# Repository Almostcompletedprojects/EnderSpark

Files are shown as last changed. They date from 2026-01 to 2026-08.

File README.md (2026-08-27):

# WireEDM

Join the discord here: https://discord.gg/86cwKxkF

Wire EDM uses electrical discharges to cut any conductive materials (brass, steel, aluminium even tungsten carbide) with no mechanical forces, enabling high precision, deep cuts, and machining of hard or delicate materials without deformation. 
This project show how to build a DIY wire EDM machine using salvaged components from an old 3D printer and other affordable parts, keeping the total cost around 250€ + 4 machined parts the ender 3 and less than 50h of work (if everything goes right).

The machine's motion system is just an Ender 3  with 1:51 gear reductions on the X and Y axes. This is required for EDM because it's a slow process and and NEMA 17 on their own are too fast.
A Raspberry Pi Pico with a TC4428 and a powerful MOSFET are used to switch up to 10A at 60KHz

The toolpath generation is simplified to be user friendly and a small tutorial is available on this video: https://youtu.be/iLnna7q0drs?si=ul4SjGQGCm429spJ

And a complete tutorial will be added on the same channel in a few months.

The conversion from a 3D printer to a wire EDM can be done in 6 steps:
- Mechanical modifications
- Wire feeder
- Firmware update
- Ark generator
- Water loop
- Fusion 360 post processor

The overall cost is about 225€ without the 3D printer separated in 3 cathegories:
- Electronics ~50€ + the power supply ~50€
- Mechanical parts ~115€
- Water managment ~80€

All required filles are/will be availlable here:
- Firmware for ender3V2 and modification lists here [List](Firmware/Modifications_list)
- [Post processor for fusion 360](Code/EnderSpark.cps)
- [GRBL files](PCB/Gerber_Enderspark_PCB_Enderspark_2_2026-01-28.zip) and [design files](PCB) with screenshots
- Mechanicals parts as .STEP (so you can modify it) are not up to date but will be availlable [here](step_files)
- .svg files to laser cut the [water container](Parts/Water-container.svg)

# WARNiNGS
The voltage is higher than the SELV in wet conditions, I don't know exactly how dangerous it is but please consider that it's a lethal risk and prepare yourself accordingly. If you don't know what your doing please don't try to replicate this project.



Copper is considered as a heavy metal, the best way to deal with the dirty water is to let it sit for a while in a ventilated area to evaporate all the water, after that it's jsut metal powder and can be disposed in the local recycling center.

This machine can generate a lot of EMF, it can be an issue if you have a heart assistance and it can perturb some electronics. Smartphones laptop and expensive stuff are usually safe but the screen of the ender 3 is glitching a lot, it's just the screen not the control so nothing to worry about.

# Mecanical parts
## Motion

| Part | Quantity | Cost per lot |
|- | - | - |
| Linear rail MGN12H 300mm | 1 | 10€ |
| Screws | 50 | 10€ |
| lead screw (T8,2mm picth, 2mm lead)| 2 | 15€ |
| Anti backlash nut | 2 | 3€ |
| GT2 pulley 60teeth 8mm bore | 2 | 3€ |
| Belts | 2 | 4€ |
| Hybrid bearings | 2 | 12€ |
| Bearings | 4 | 4€ |
| PLA 200g | 1 | 4€ |
| Aluminium parts | 1 | 50€ |
| Total |  | 115€ |

A big advantage of wire EDM compared to CNC milling is that the frame doesn't need to be very stiff, the hardware just need to support the wire feeder on the X axis and the water tank ~4kg on the Y axis. The Z axis isn't used during the cutting process but it's quite usefull to help changing the wire.

I've added a linear rail (MGN12H) on X axis, another can be requiered on Y depending on your version, if the Y carriage feels strong with the regular rollers you don't need any change. The rail is bolted directly on X axis with T nuts and for the why axis you need to drill 4 holes in the buildplate support, thats all.

Wire EDM can be very slow depending on the thickness so one of the most important requirement is to be able to move slowly at a fixed rate. Regular stepper motors aren't able to do that even with microstepping. The best solution is to convert both axis to lead screw + 1:3 belt reducer with a 2GT pulley and a 2mm pitch 2 mm lead T8 lead screw and anti-backlash nuts (the plastic ones works fine).
They cost 20€ each and have some backlash so it's far from the best solution.

## Wire feeder

The wire feeder is the only complicated part which need to be custom made because it needs to fullfill a few requierments:
- Stifness, during the cutting process the arcs can generate vibrations, to achieve a good surface finish the wire need to be very straight
- Electrically insulated, even if the cutting is done under de-ionised water, some electrolysis can occur which can reduce the power output. An insulated feeder also prevent from shorts if a metal part fall between the wire and the feeder
- Grounded, at 60kHz the long wire is a big antenna which can emit a lot of parasites and damage electronics. Grounding as much part as possible is crucial to avoid that (and any risk for pacemaker users)
- Tensionner mechanism, to avoid wire vibration the wire need to be adequatly tensionned.
- Waste spool, wire edm consume the workpiece AND the wire, depending on the material it can use a lot of wire
- Hard wire guide, I you have an old ender 3 you've probably experience filament grinding the extruder even if its plastic against plastic, the same thing can happend here with soft brass



This is the CAD of the second version, the extruder (nema 17 + a brass cylinder) is pulling the wire all the way from the tensionner. 
The tensionner conssit of two ball bearing pressing into each other like a 3D printer extruder, the sping can be adjust to block more the wire and provide more tension.
A standard value of tension for a 0.25mm wire is 18N, I don't have an easy way to measure it for now. Maybe I can link the tension with the resonance frequency and use an audio app for calibration.

Then, the wire need to be guided very precisely, for the upper guide I use an off the shelf rubis nozzle. A water jet is used to evacuate the chips, the nozzle is printed in pla, the pressure is not that high. The lower guide is a ceramic ball bearing with a PLA spacer and a .4mm brass nozzle to push the wire against the spacer. The two other ball bearings (ceramic for the lower one and steel with plastic cover for the upper one) just guide the wire to the extruder.

The ball bearings needs to be in ceramic for three reason:
1. Corosion
2. No lubricant can desovle in water
3. High hardness
4. Electrical insulation 

The wire is connected to the (-) terminal of the PSU by the brass wheel and in the future a tungsten carbide contact block, but since the wire emit EMF like an antenna, I want to ground as much metal as I can, so the whole motor assembly is at the same potential as the wire, but the frame of the printer and the red part are grounded. The voltage arent high so a layer of epoxy or an anodization is enougth to insulate the two regions.



The first version on the left use a lots of printed parts, it works but the tensionner some part can flex and reduce the wire tension/straightness so I made a second version in 5mm thick alluminium plate with 10mm thick tensionners.

All the parts are availlable in .sldprt and .step

### Manufcaturing

Both the red and orange parts are 5mm thick aluminium cutted with my homemade CNC with a 3.175mm single flute endmill, the geometry is a bit complex and can be improve but if you want to make it there is a catch. The two parts are electrically insulated and need to be very straight, there is two options for insulating metalic coating. 
- Anodisation of aluminium + galvanic varnish, it requier sulfuric acid and other chemicals and it's not that easy to make a thick and strong coating
- Powder coating for a steel frame, very durable and steel is stiffer than aluminium.

Both can be DIY or custom made by a company like JLCPCB especially in the case of powder coating. 

The two other aluminium parts doesn't need any coating same for the brass wheel, it's just a cylinder with 3 holes.

### Spool

Wire edm as you can guess consume wire, so I need a simple way to manage the waste wire. My solution is to have the new spool of wireconnected to the waste spool with magnet so the second one can be drived by the first one. Since the first spool will get smaller and smaller and the second bigger and bigger, the first one will have to turn way fater to maintain a tension. With this configurtion, the first spool has a way smaller inner diameter which made it spin fzster at any moment. The magnets act like a clutch to maintain constant load at variable speeds.



# Electronics
## generator

[Part list](Parts/Part_list_electronics.xlsx)

It's actually pretty easy to make an arc for EDM, it won't be as powerfull as a commercial machine but pretty close. We just need to switch a powerfull MOSFET on and of very fast, I use the IRF135B203 wich can handle 135V 129A and 500A peak. A freewheel diode is placed in parallel of the arc to protect the mosfet from reverse current generated by the inductance of the wire. The mosfet is drived by a TC4428 with a schotcky diode to protect the IC a square pwm signal is generated by the pi pico, the pico code is optimised to generate the wave as fast as possible. We also have a DC-DC converter because we need 12V to drive this mosfet. I measure the voltage accross the power resistor with 2 divider which gives me the average current in the resistor and the voltage charge of the capacitors. The close loop controle is based on the average current, if it's lower than a defined value we increase the speed otherwise we're slowing down. If the capacitor voltage is dropping, we slow down dramatically and if it's low for more than 5s the process is stopped.
The gerber files are available [here](PCB/Gerber_Enderspark_PCB_Enderspark_2_2026-01-28.zip) with [design files](PCB), the requiered components are listed [here](Parts/Part_list_electronics.xlsx) the design requier no vias so you can DIY it but if you're laizy like me you can order it to JLCPCB

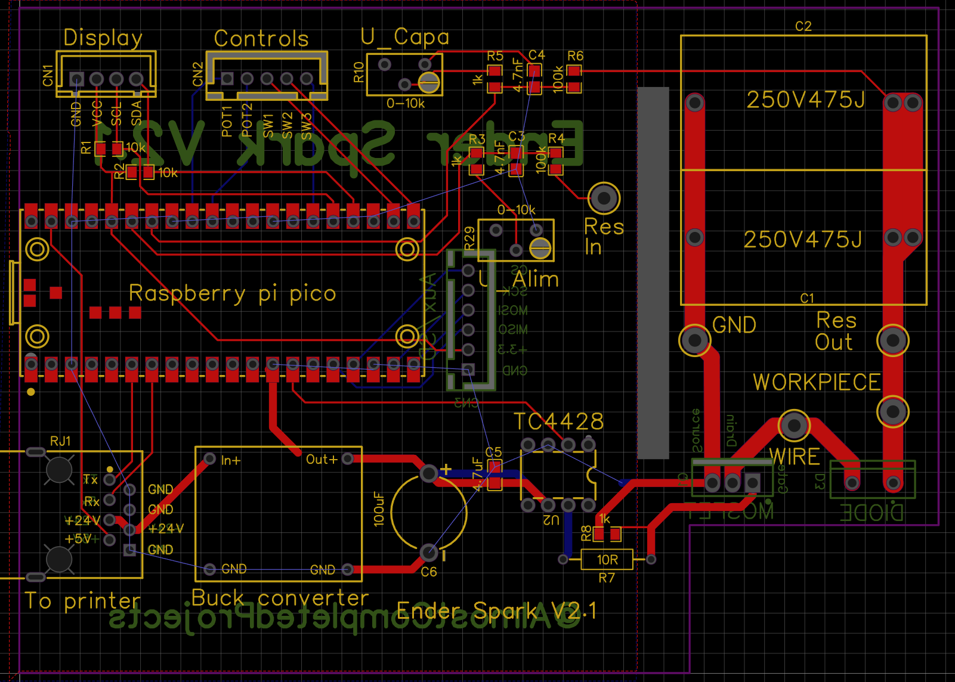
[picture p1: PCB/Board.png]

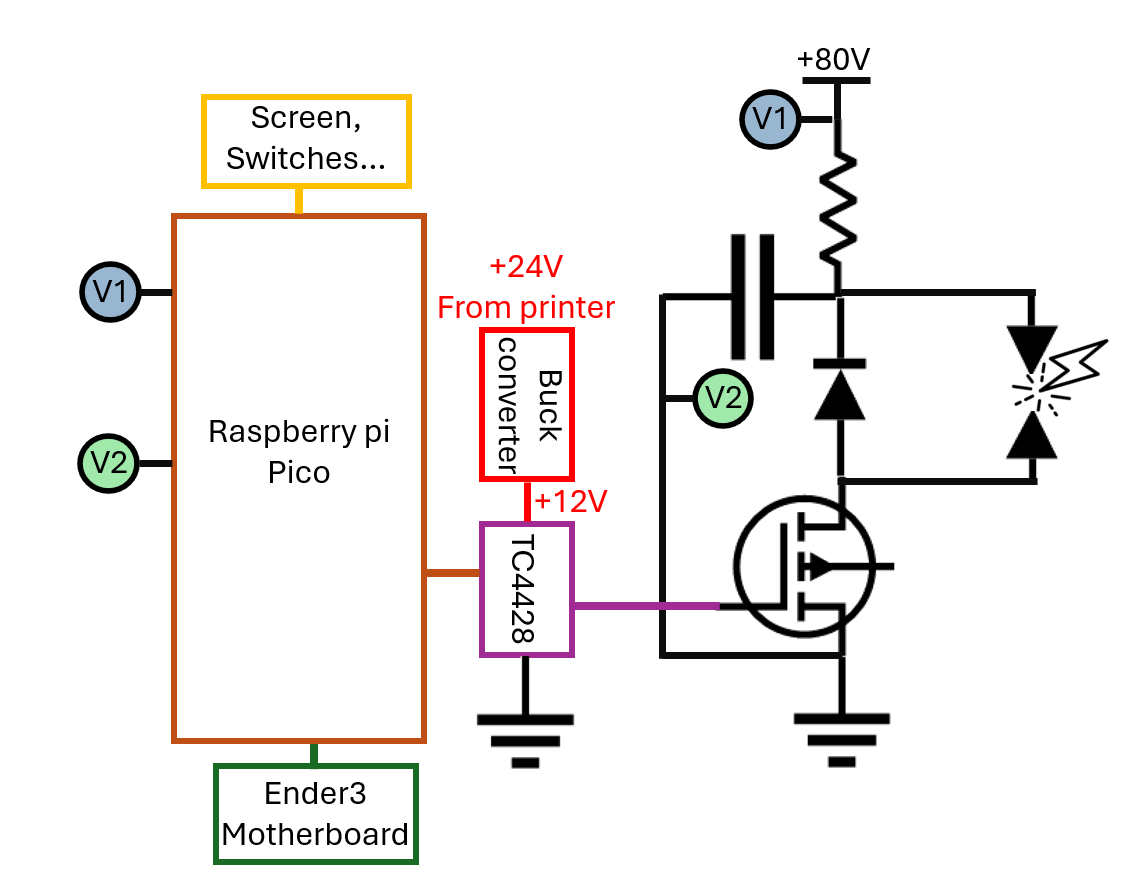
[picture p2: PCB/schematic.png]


## Power managment 

The power supply should be able to deliver at least 5A, 48V is enougth to cutt alluminium but a higher voltager means a higher energy stored in the capacitors (E = 1/2C U²). If you plan to cut copper or steel you can buy a switch mode power supply with adjustable output (mine can go up to 110V).

In the best case scenario, each pulse will create an arc and remove some matter but in realitty sometimes the wire is too far to create a spark and sometimes the wir eis in direct contact and will create a (momentary) short circuit. A short can be detected by the voltage/current measurement and if so the cutting is stopped.

Last part is the capacitors, it helps deliver high current durring short amount of time. You can't use some standard electrolitic capacitor (belive me I tried) ceramic is a good option but we need very low ESR so polymer is the only suitable option. In my setup I use 2x 4.7uF in parallel so ~10uF rated for 200V.

# Water

| Part | Quantity | Cost per lot |
|- | - | - |
| 24V membrane pump | 1 | 15€ |
| PC/PS/PMMA plate 50X50X5mm | 1 | 15€ |
| PM12 pneumatic connector | 1 | 5€ |
| OD12 ID10 PVC tube | 3m | 5€ |
| Bottle filter 10" | 1 | 20€ |
| Filter cardrige | 1 | 5€ |
| 1/2" -> 10mm barbed fitting | 1 | 2€ |
| PC6 M8x1.25 connector | 1 | 3€ |
| 6mm pneumatic pipe | 2m | 3€ |
| 4mm silicone tube | 0.5m | 1€ |
| Silicone seal cartridge | 1 | 5€ |
| Total |  | 80€ |

The EDM process must be done under a dielectric fluid, it can be ethanol, oil or kerosene but the easyest solution is obviously deionised water. Water is also used for cooling (the electrical components and the workpiece) and chip evacuation. The "builtplate" is a water tank made out of acrily sheets welded with aceton and a bit of silicone for etancheity. I've also add a steel shit so I can quickly remove it from my magnetic buildplate.

EDM generate a ton of small metalic particles which needs to be filter during the cutting, The best pump I've found is a membrane pump which can provide high pressure (necessary for good filtration) and is quite silent when underpowered, it's design for 24V and I power it between 5-7V depending on the material. The filter is a standard polyester coton filter <0.1um in a cardrige in the future I'll probably try washables filters like ceramic or stainless steel. I use push pull and 6mm tubes for all my connection except for the nozzle its a 4mm.

After each cuts I put the deionised water in it's original tank for decantation, and separate the "pure" water from the dirty one a few days later.

Copper is consiered as a heavy metal, the best way to deal with the dirty water is to let it sit for a while in a ventilated area to evaporate all the water, after that it's jsut metal powder and can be disposed in the local recycling center.

The water VAT was generated with:
https://www.makercase.com/basicBox

# Firmware modifications
A few modifications of the firmware are requiered and listed [here](Firmware/Modifications_list)
The configuration.h, configuration_adv.h and pins.h for an ender3V2 are also availlable [Ender3V2](Firmware/Ender3V2)

Basically we disable everything related to temperature management, enable UART2 to communicate with the pi pico (which require 2 precise solders and 2 traces cut on the motherboard).
We also need to configure a second output fan which can be enabled by M106 for the waterpump on the old output port of the nozzle. 

# Toolpath generation

The two easiest ways to generate a gcode is with a slicer or with a cam plugin. I've tried kirimoto which have a wire edm mode but there's very little features and you can't control the extruder. I've also tried cura, the limitation is that you can't set a very small speed, I even tried modifiyng the software but I coulnd'nt find a solution, maybe with orca slicer?

In my opinion the easyest solution is to use the CAM part of fusion 360 with the laser/waterjet mod. 



It's easy to setup a waterjet tool with 0.3mm stream and you can add a very long lead in to enter the workpiece from anywhere. You don't have to worry about feeds and speeds here, you just need to set all the hight to zero to avoid Z movements, and set up the appropriate thickness.



Then you need to select the wire edm [post processor for fusion 360](Code/EnderSpark.cps), I modified the wazer post processor to match my needs, I will not detail it here, the file is in this folder, you just have to paste it in the appropriate location.

I have a very small database for differents materials, so if the thickness is right, just selec the material and it should be good to go. It's an ongoing project soyou will probably have sligly differents settings than me, I'll recommand you to do a speedtest for the material you're planing to cut and modify the database:



surfacespeed is the speed in mm²/min, which correspond to the linear speed for a defined thickness ex: 3mm/min for 10mm thick aluminium is 30mm²/min.
wirespeedpermm is the wire consumed per mm² with the previous example of 30mm²/min and 25mm it will consume 750mm of wire to cut this amount of material in 1min.

A cheap 100m of 0.2mm joaillery brass wire (2€) will last for more than two hours ~0.02€/m, a more expensive 5kg of edm 0.25mm brass wire (110€) is almost 12km so ~0.01€/m and 250h of use.
In the future I will try molybdenum wire which is just a bit more expensive but it can be used several times but I need to design a back and forth drive.

Some more commun supply are also needed like heat shrink tube, solder, wires (I use wires from old RJ45 cable it can handle something like 5A without a problem, its free nd easly accessible).

A lots of tools are needed to work properly:

- Soldering iron
- Drill press
- Caliper
- Dial indicator
- Heat gun
- A good square rule
- Handed metal saw 
- Metal band saw (if your alumiun extrusions needed to be with a perfect 90° angle)
- Hand drill
- Center punch
- Marker for metal
- Hammer, clamps, screw drivers others hand tools
- 3D printer
- deburr tool

# License

This project (CAD files, models, schematics, and associated code) is licensed under the **[CERN-OHL-S-v2](LICENSE)** (CERN open Hardware License Version 2 strongly reciprocal)
- **Freedom to build and modify:** You are free to manufacture, study, modify, and distribute this machine, including for commercial purposes.
- **Strong Copyleft / Reciprocity:** If you modify these designs or code and distribute/sell a product based on them, **you must make all modified source files publicly available under this same license (CERN-OHL-S v2)**.
- **No warranty:** Provided "as-is" without warranty of any kind.

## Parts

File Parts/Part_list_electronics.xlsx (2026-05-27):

Board
Type | Quantity | cost | total | link
Raspberry pi pico | 1 | 4.0 € | 4 € | https://fr.aliexpress.com/item/1005008244091735.html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
TC4428 | 5 | 0.4 € | 2 € | https://fr.aliexpress.com/item/1005006912580387.html
IRF135B203 (or similar) | 10 | 0.5 € | 5 € | https://fr.aliexpress.com/item/1005010049039273.html
4.7uF polymer capacitor 250V475J | 10 | 0.3 € | 3 € | https://fr.aliexpress.com/item/1005005691512866.html
Kit smd capacitors 0805 | 1 | 3.0 € | 3 € | https://fr.aliexpress.com/item/1005010314674256.html
kit smd resistors 0805 | 1 | 2.0 € | 2 € | https://fr.aliexpress.com/item/1005009735103526.html
RJ45 connector | 10 | 0.2 € | 2 € | https://fr.aliexpress.com/item/1005004004680555.html?curPageLogUid=za5Vf5sJza7y
Freewheel diode MUR820 | 10 | 0.4 € | 4 € | https://fr.aliexpress.com/item/1005008518514945.html
Headers | 1 | 2.0 € | 2 € | https://fr.aliexpress.com/item/1005007414089348.html
Buck converter 24->12V | 1 | 3.0 € | 3 € | https://fr.aliexpress.com/item/1005010728500684.html
JST connectors kit | 1 | 4.0 € | 4 € | https://fr.aliexpress.com/item/1005009532866035.html?curPageLogUid=rzWAHQcZNLAA
Aviation connector M12 4P | 1 | 6.0 € | 6 € | https://fr.aliexpress.com/item/1005006373729951.html
2mm banan connectors m+f | 6 | 0.2 € | 1.2 € | https://fr.aliexpress.com/item/1005006400659486.html
2mm banan connectors f wall | 10 | 0.4 € | 4 € | https://fr.aliexpress.com/item/1005009568396783.html?curPageLogUid=LpgjQQSx0yEq
Oled screen | 1 | 2.5 € | 2.5 € | https://fr.aliexpress.com/item/1005004355547926.html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
potentiometer 10K 10turns | 10 | 0.1 € | 1 € | https://fr.aliexpress.com/item/1005005916886477.html?curPageLogUid=35UUVdYZaxof
Aluminum box | 1 | 13.0 € | 13 € | https://fr.aliexpress.com/item/1005007982863933.html
0-80V power supply 600W | 1 | 42.0 € | 42 € | https://fr.aliexpress.com/item/1005008735760315.html?curPageLogUid=so0ryaD20kcC
 |  |  | 103.7 €

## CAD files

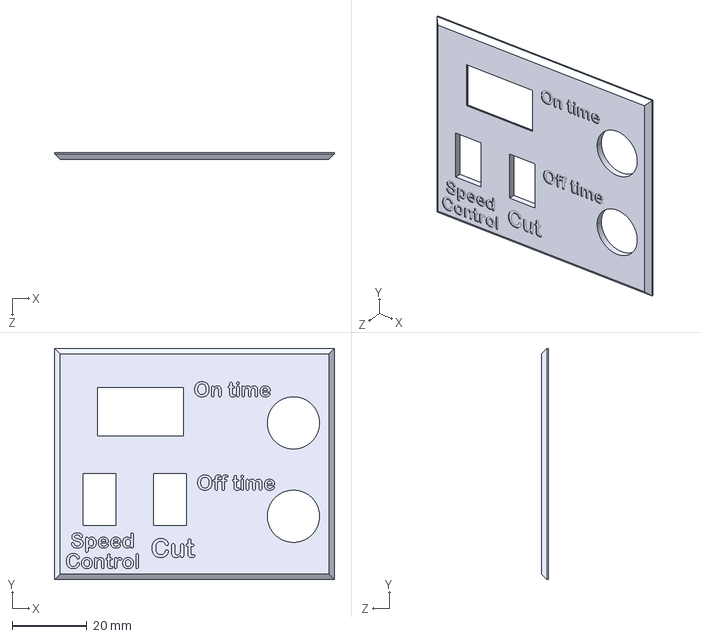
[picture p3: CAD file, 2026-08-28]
Parts/Printed parts/Board/text plate.STEP
75.0 x 62.0 x 1.90 mm

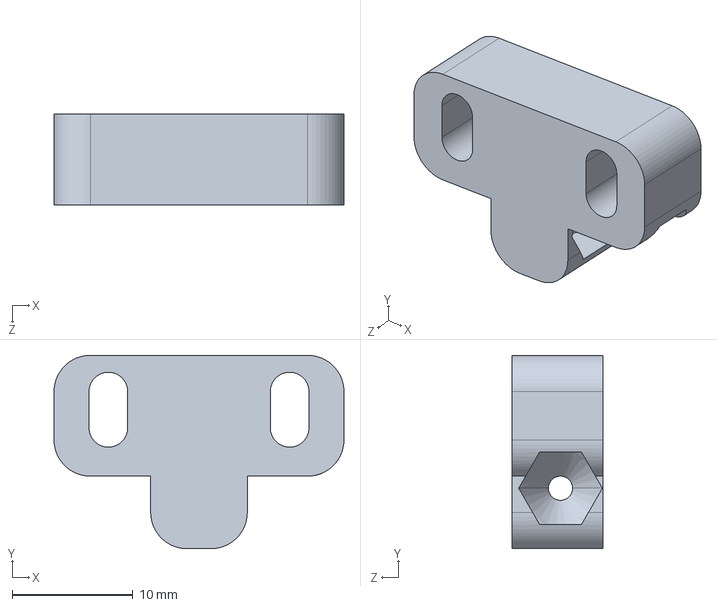
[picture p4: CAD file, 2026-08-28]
Parts/Printed parts/Head/wire guide brass.STEP
24.0 x 16.0 x 7.50 mm

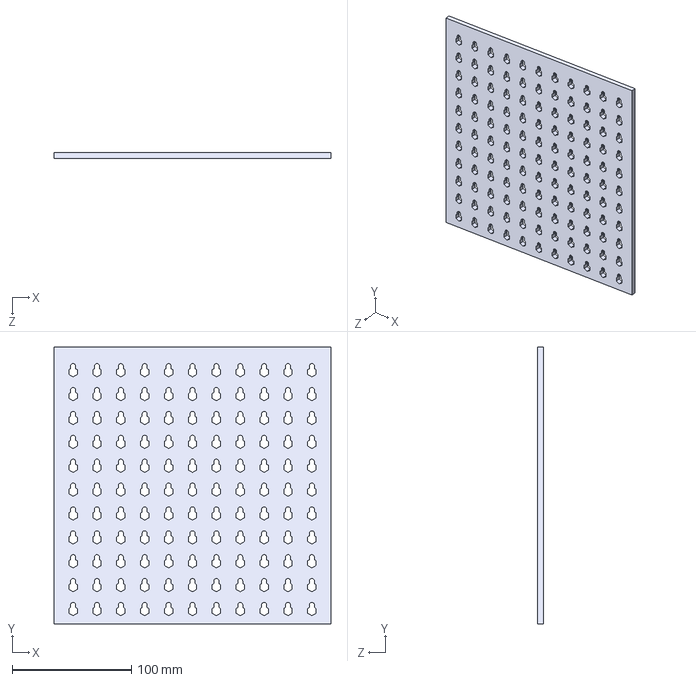
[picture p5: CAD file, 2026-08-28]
Parts/Printed parts/Tank/Plate.STEP
232.0 x 232.0 x 5.00 mm

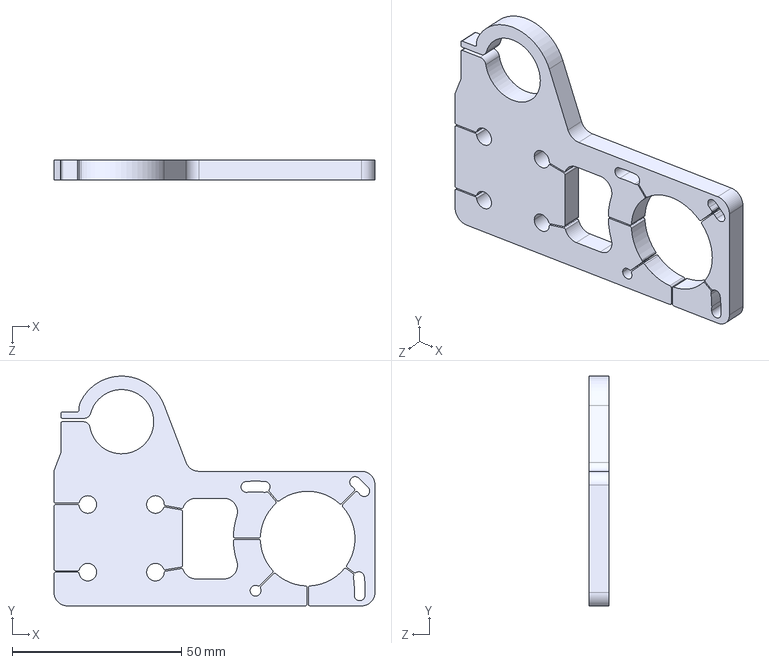
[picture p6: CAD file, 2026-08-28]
Parts/Sheetmetal/y bearing +motor holder ender 3v2_alu.STEP
95.0 x 68.0 x 6.00 mm

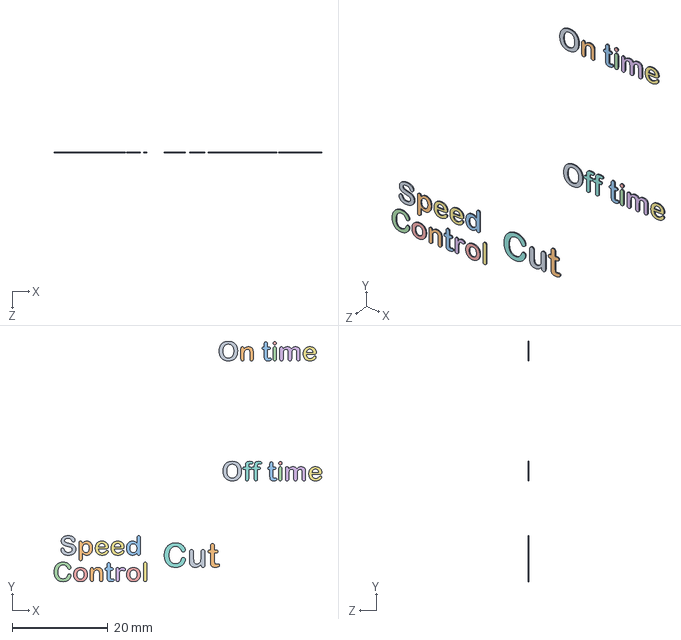
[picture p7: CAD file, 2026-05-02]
Parts/Printed parts/Board/aluminium box_text.STEP
55.8 x 50.1 x 0.2 mm

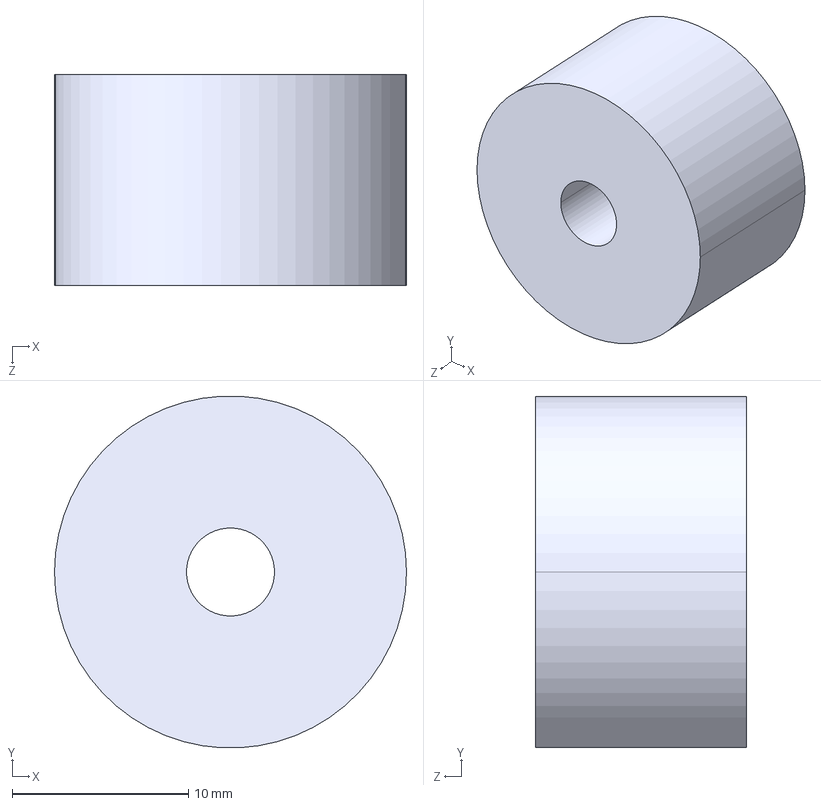
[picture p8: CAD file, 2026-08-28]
Parts/Printed parts/Head/spacer.STEP
20.0 x 20.0 x 12.0 mm

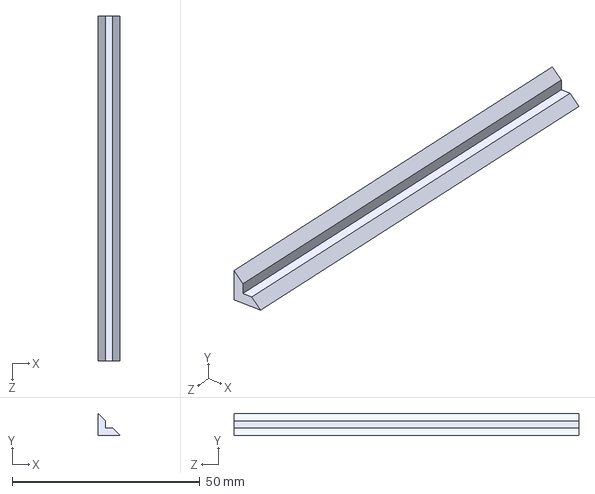
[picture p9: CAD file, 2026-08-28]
Parts/Printed parts/Tank/equereinterne.STEP
6.00 x 6.00 x 92.0 mm

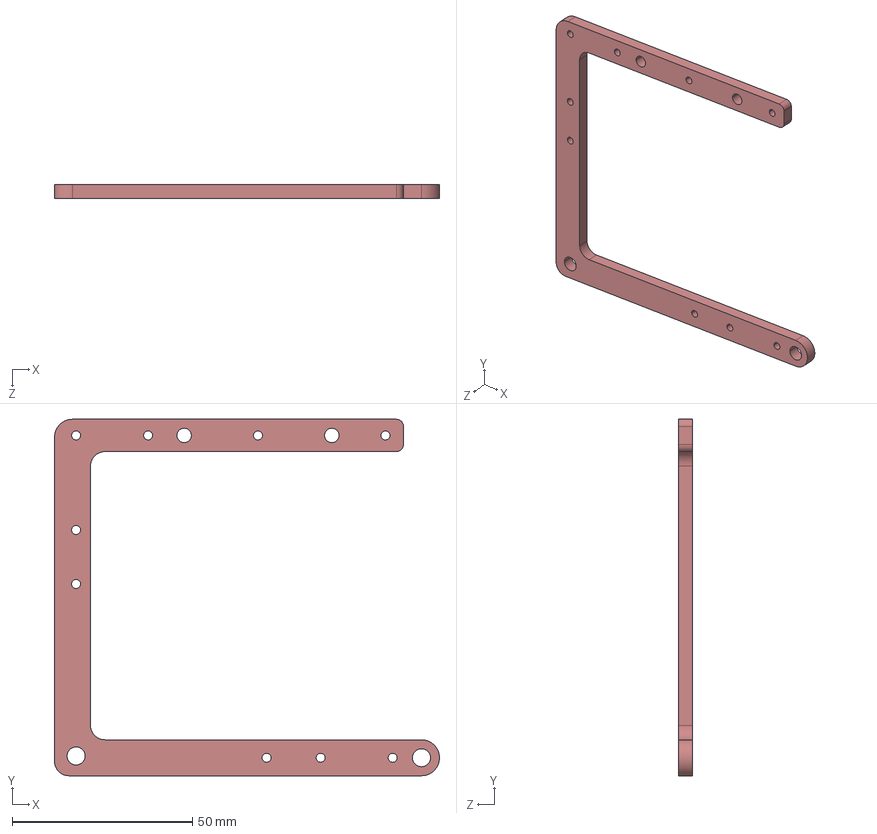
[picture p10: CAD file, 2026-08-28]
Parts/Sheetmetal/Steel framev5.STEP
106.9 x 99.0 x 4.00 mm

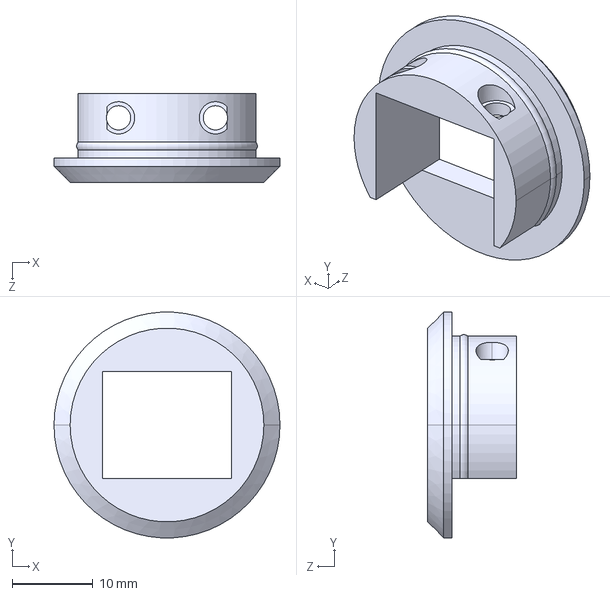
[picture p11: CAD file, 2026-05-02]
Parts/Printed parts/Board/rj45plug.STEP
28.0 x 28.0 x 11.0 mm

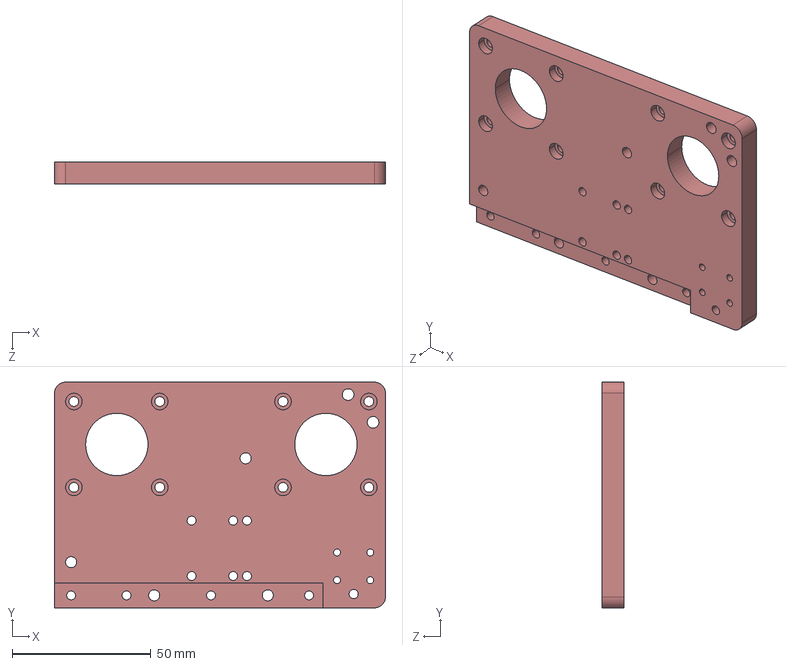
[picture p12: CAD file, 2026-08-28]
Parts/Printed parts/Head/plastic framev5.STEP
119.5 x 81.5 x 8.00 mm

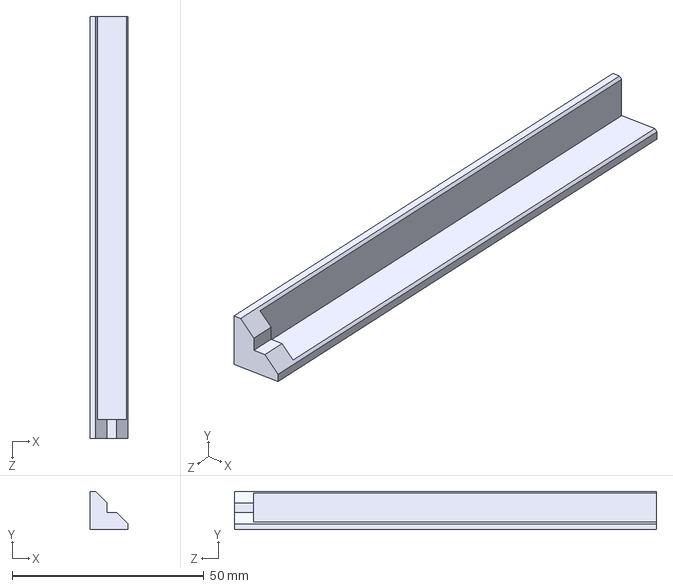
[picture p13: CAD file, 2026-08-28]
Parts/Printed parts/Tank/Equerre.STEP
10.00 x 10.0 x 110.0 mm

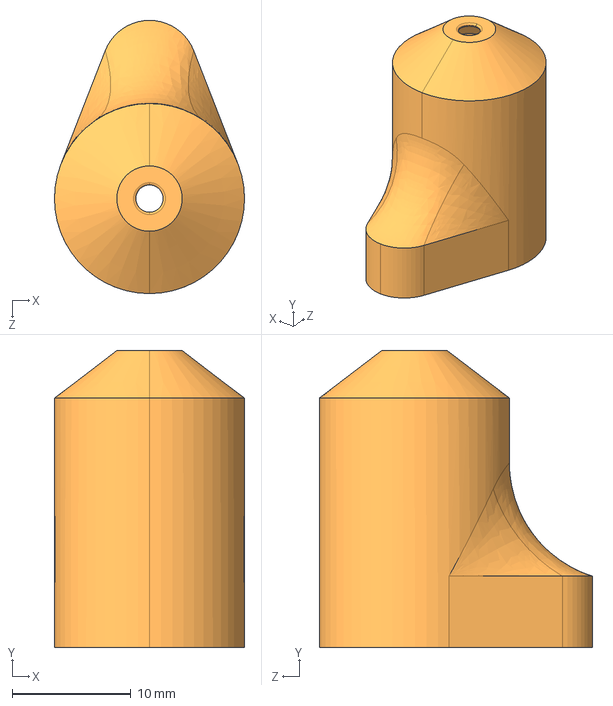
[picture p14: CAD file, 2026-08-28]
Parts/Printed parts/Head/water_nozzle.STEP
16.0 x 25.0 x 23.0 mm

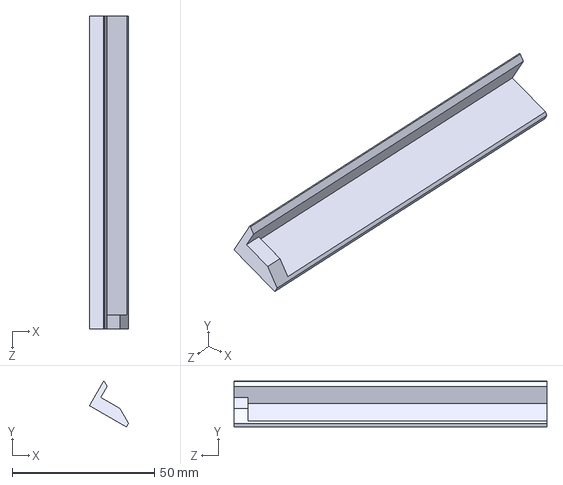
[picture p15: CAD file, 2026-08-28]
Parts/Printed parts/Tank/equerrere60.STEP
13.7 x 16.2 x 110.0 mm

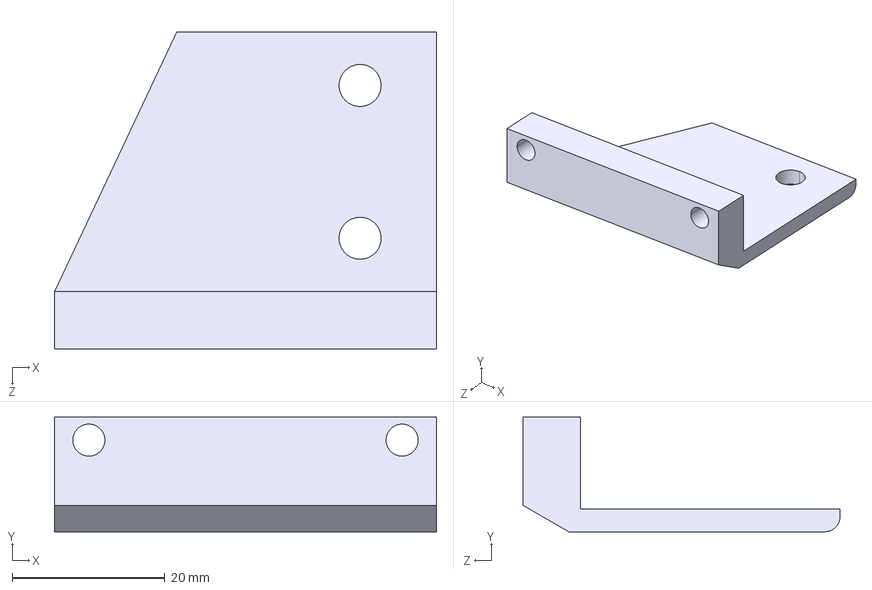
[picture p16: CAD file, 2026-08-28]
Parts/Printed parts/Head/xcarriage for v2.STEP
50.0 x 15.0 x 41.5 mm

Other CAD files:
Parts/Printed parts/Tank/2020test.STEP
Parts/Printed parts/Head/y bearing holder ender 3v2_alu.STEP
Parts/Printed parts/Head/y bearing holder b.STEP
Parts/Printed parts/Head/X motor support.STEP
Parts/Printed parts/Head/Tr8x2 nut set.STEP
Parts/Printed parts/Head/xbearingholder left.STEP
Parts/Printed parts/Head/xbearingholder right.STEP
Parts/Printed parts/Head/y bearing +motor holder ender 3v2.STEP
Parts/Printed parts/Head/y bearing holder ender 3v2.STEP

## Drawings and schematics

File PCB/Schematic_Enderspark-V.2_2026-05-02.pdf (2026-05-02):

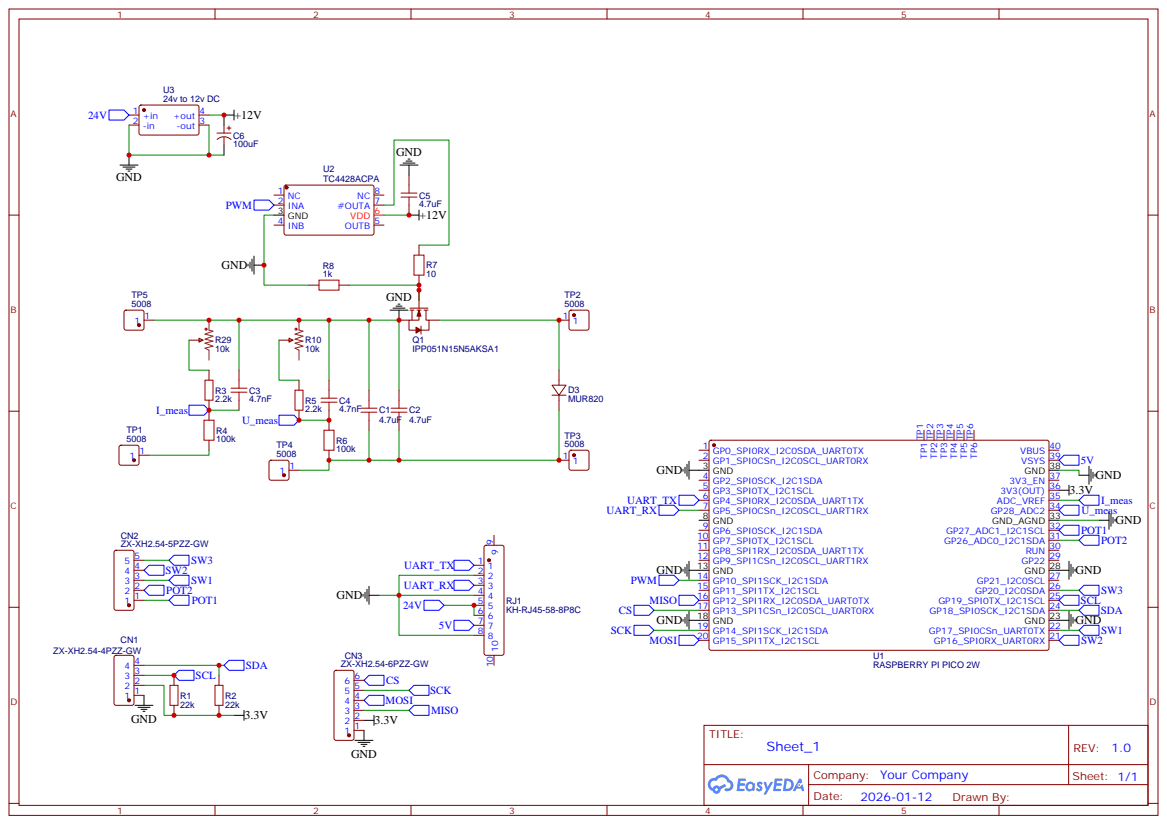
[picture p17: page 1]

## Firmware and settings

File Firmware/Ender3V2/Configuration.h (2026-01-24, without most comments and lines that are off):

#pragma once
#define CONFIG_EXAMPLES_DIR "Creality/Ender-3 V2/CrealityV422/MarlinUI"
#define CONFIGURATION_H_VERSION 02010206
#define STRING_CONFIG_H_AUTHOR "(none, default config)" // Who made the changes.
#define SHOW_BOOTSCREEN
  #define MOTHERBOARD BOARD_CREALITY_V4
#define SERIAL_PORT 2
#define BAUDRATE 115200
#define CUSTOM_MACHINE_NAME "Ender-3 V2"
#define X_DRIVER_TYPE TMC2208_STANDALONE
#define Y_DRIVER_TYPE TMC2208_STANDALONE
#define Z_DRIVER_TYPE TMC2208_STANDALONE
#define E0_DRIVER_TYPE TMC2208_STANDALONE
#define EXTRUDERS 1
#define DEFAULT_NOMINAL_FILAMENT_DIA 1.75
#define TEMP_SENSOR_0 999
#define TEMP_SENSOR_1 0
#define TEMP_SENSOR_2 0
#define TEMP_SENSOR_3 0
#define TEMP_SENSOR_4 0
#define TEMP_SENSOR_5 0
#define TEMP_SENSOR_6 0
#define TEMP_SENSOR_7 0
#define TEMP_SENSOR_BED 998
#define TEMP_SENSOR_PROBE 0
#define TEMP_SENSOR_CHAMBER 0
#define TEMP_SENSOR_COOLER 0
#define TEMP_SENSOR_BOARD 0
#define TEMP_SENSOR_REDUNDANT 0
#define DUMMY_THERMISTOR_998_VALUE  50
#define DUMMY_THERMISTOR_999_VALUE 200
#if TEMP_SENSOR_IS_MAX_TC(0)
  #define MAX31865_SENSOR_OHMS_0      100 // (Ω) Typically 100 or 1000 (PT100 or PT1000)
  #define MAX31865_CALIBRATION_OHMS_0 430 // (Ω) Typically 430 for Adafruit PT100; 4300 for Adafruit PT1000
#endif
#if TEMP_SENSOR_IS_MAX_TC(1)
  #define MAX31865_SENSOR_OHMS_1      100
  #define MAX31865_CALIBRATION_OHMS_1 430
#endif
#if TEMP_SENSOR_IS_MAX_TC(2)
  #define MAX31865_SENSOR_OHMS_2      100
  #define MAX31865_CALIBRATION_OHMS_2 430
#endif
#if HAS_E_TEMP_SENSOR
  #define TEMP_RESIDENCY_TIME         10  // (seconds) Time to wait for hotend to "settle" in M109
  #define TEMP_WINDOW                  1  // (°C) Temperature proximity for the "temperature reached" timer
  #define TEMP_HYSTERESIS              3  // (°C) Temperature proximity considered "close enough" to the target
#endif
#if TEMP_SENSOR_BED
  #define TEMP_BED_RESIDENCY_TIME     10  // (seconds) Time to wait for bed to "settle" in M190
  #define TEMP_BED_WINDOW              1  // (°C) Temperature proximity for the "temperature reached" timer
  #define TEMP_BED_HYSTERESIS          3  // (°C) Temperature proximity considered "close enough" to the target
#endif
#if TEMP_SENSOR_CHAMBER
  #define TEMP_CHAMBER_RESIDENCY_TIME 10  // (seconds) Time to wait for chamber to "settle" in M191
  #define TEMP_CHAMBER_WINDOW          1  // (°C) Temperature proximity for the "temperature reached" timer
  #define TEMP_CHAMBER_HYSTERESIS      3  // (°C) Temperature proximity considered "close enough" to the target
#endif
#if TEMP_SENSOR_REDUNDANT
  #define TEMP_SENSOR_REDUNDANT_SOURCE    E1  // The sensor that will provide the redundant reading.
  #define TEMP_SENSOR_REDUNDANT_TARGET    E0  // The sensor that we are providing a redundant reading for.
  #define TEMP_SENSOR_REDUNDANT_MAX_DIFF  10  // (°C) Temperature difference that will trigger a print abort.
#endif
#define HEATER_0_MINTEMP   0
#define HEATER_1_MINTEMP   5
#define HEATER_2_MINTEMP   5
#define HEATER_3_MINTEMP   5
#define HEATER_4_MINTEMP   5
#define HEATER_5_MINTEMP   5
#define HEATER_6_MINTEMP   5
#define HEATER_7_MINTEMP   5
#define BED_MINTEMP        0
#define CHAMBER_MINTEMP    5
#define HEATER_0_MAXTEMP 275
#define HEATER_1_MAXTEMP 275
#define HEATER_2_MAXTEMP 275
#define HEATER_3_MAXTEMP 275
#define HEATER_4_MAXTEMP 275
#define HEATER_5_MAXTEMP 275
#define HEATER_6_MAXTEMP 275
#define HEATER_7_MAXTEMP 275
#define BED_MAXTEMP      120
#define CHAMBER_MAXTEMP  60
#define HOTEND_OVERSHOOT 15   // (°C) Forbid temperatures over MAXTEMP - OVERSHOOT
#define BED_OVERSHOOT    10   // (°C) Forbid temperatures over MAXTEMP - OVERSHOOT
#define COOLER_OVERSHOOT  2   // (°C) Forbid temperatures closer than OVERSHOOT
#define PIDTEMP           // See the PID Tuning Guide at https://reprap.org/wiki/PID_Tuning
#define PID_MAX  255      // Limit hotend current while PID is active (see PID_FUNCTIONAL_RANGE below); 255=full current
#define PID_K1     0.95   // Smoothing factor within any PID loop
    #define DEFAULT_KP  28.72
    #define DEFAULT_KI   2.62
    #define DEFAULT_KD  78.81
#define MAX_BED_POWER 255 // limits duty cycle to bed; 255=full current
#define PIDTEMPBED
  #define DEFAULT_BED_KP 462.10
  #define DEFAULT_BED_KI  85.47
  #define DEFAULT_BED_KD 624.59
#define MAX_CHAMBER_POWER 255 // limits duty cycle to chamber heater; 255=full current
  #define PID_FUNCTIONAL_RANGE 10 // If the temperature difference between the target temperature and the actual temperature
#define PREVENT_LENGTHY_EXTRUDE
#define EXTRUDE_MAXLENGTH 1000
#define USE_XMIN_PLUG
#define USE_YMIN_PLUG
#define USE_ZMIN_PLUG
#define ENDSTOPPULLUPS
#define X_MIN_ENDSTOP_INVERTING false // Set to true to invert the logic of the endstop.
#define Y_MIN_ENDSTOP_INVERTING false // Set to true to invert the logic of the endstop.
#define Z_MIN_ENDSTOP_INVERTING false // Set to true to invert the logic of the endstop.
#define I_MIN_ENDSTOP_INVERTING false // Set to true to invert the logic of the endstop.
#define J_MIN_ENDSTOP_INVERTING false // Set to true to invert the logic of the endstop.
#define K_MIN_ENDSTOP_INVERTING false // Set to true to invert the logic of the endstop.
#define U_MIN_ENDSTOP_INVERTING false // Set to true to invert the logic of the endstop.
#define V_MIN_ENDSTOP_INVERTING false // Set to true to invert the logic of the endstop.
#define W_MIN_ENDSTOP_INVERTING false // Set to true to invert the logic of the endstop.
#define X_MAX_ENDSTOP_INVERTING false // Set to true to invert the logic of the endstop.
#define Y_MAX_ENDSTOP_INVERTING false // Set to true to invert the logic of the endstop.
#define Z_MAX_ENDSTOP_INVERTING false // Set to true to invert the logic of the endstop.
#define I_MAX_ENDSTOP_INVERTING false // Set to true to invert the logic of the endstop.
#define J_MAX_ENDSTOP_INVERTING false // Set to true to invert the logic of the endstop.
#define K_MAX_ENDSTOP_INVERTING false // Set to true to invert the logic of the endstop.
#define U_MAX_ENDSTOP_INVERTING false // Set to true to invert the logic of the endstop.
#define V_MAX_ENDSTOP_INVERTING false // Set to true to invert the logic of the endstop.
#define W_MAX_ENDSTOP_INVERTING false // Set to true to invert the logic of the endstop.
#define Z_MIN_PROBE_ENDSTOP_INVERTING false // Set to true to invert the logic of the probe.
#define ENDSTOP_INTERRUPTS_FEATURE
#define DEFAULT_AXIS_STEPS_PER_UNIT   { 4000, 4000, 400, 250 }
#define DEFAULT_MAX_FEEDRATE          { 500, 500, 5, 25 }
#define DEFAULT_MAX_ACCELERATION      { 500, 500, 100, 1000 }
#define DEFAULT_ACCELERATION           500    // X, Y, Z and E acceleration for printing moves
#define DEFAULT_RETRACT_ACCELERATION   500    // E acceleration for retracts
#define DEFAULT_TRAVEL_ACCELERATION   1000    // X, Y, Z acceleration for travel (non printing) moves
#define CLASSIC_JERK
  #define DEFAULT_XJERK 10.0
  #define DEFAULT_YJERK 10.0
  #define DEFAULT_ZJERK  0.3
#define DEFAULT_EJERK    5.0  // May be used by Linear Advance
#define Z_MIN_PROBE_USES_Z_MIN_ENDSTOP_PIN
#define PROBE_MANUALLY
#define NOZZLE_TO_PROBE_OFFSET { 10, 10, 0 }
#define PROBING_MARGIN 10
#define XY_PROBE_FEEDRATE (50*60)
#define Z_PROBE_FEEDRATE_FAST (4*60)
#define Z_PROBE_FEEDRATE_SLOW (Z_PROBE_FEEDRATE_FAST / 2)
#define Z_CLEARANCE_DEPLOY_PROBE   10 // (mm) Z Clearance for Deploy/Stow
#define Z_CLEARANCE_BETWEEN_PROBES  5 // (mm) Z Clearance between probe points
#define Z_CLEARANCE_MULTI_PROBE     5 // (mm) Z Clearance between multiple probes
#define Z_PROBE_LOW_POINT          -2 // (mm) Farthest distance below the trigger-point to go before stopping
#define Z_PROBE_OFFSET_RANGE_MIN -10
#define Z_PROBE_OFFSET_RANGE_MAX 10
#define X_ENABLE_ON 0
#define Y_ENABLE_ON 0
#define Z_ENABLE_ON 0
#define E_ENABLE_ON 0 // For all extruders
#define DISABLE_OTHER_EXTRUDERS   // Keep only the active extruder enabled
#define INVERT_X_DIR false
#define INVERT_Y_DIR false
#define INVERT_Z_DIR true
#define INVERT_E0_DIR false
#define INVERT_E1_DIR false
#define INVERT_E2_DIR false
#define INVERT_E3_DIR false
#define INVERT_E4_DIR false
#define INVERT_E5_DIR false
#define INVERT_E6_DIR false
#define INVERT_E7_DIR false
#define X_HOME_DIR -1
#define Y_HOME_DIR -1
#define Z_HOME_DIR -1
#define X_BED_SIZE 220
#define Y_BED_SIZE 220
#define X_MIN_POS 0
#define Y_MIN_POS 0
#define Z_MIN_POS 0
#define X_MAX_POS X_BED_SIZE
#define Y_MAX_POS Y_BED_SIZE
#define Z_MAX_POS 250
#define MIN_SOFTWARE_ENDSTOPS
  #define MIN_SOFTWARE_ENDSTOP_X
  #define MIN_SOFTWARE_ENDSTOP_Y
  #define MIN_SOFTWARE_ENDSTOP_Z
  #define MIN_SOFTWARE_ENDSTOP_I
  #define MIN_SOFTWARE_ENDSTOP_J
  #define MIN_SOFTWARE_ENDSTOP_K
  #define MIN_SOFTWARE_ENDSTOP_U
  #define MIN_SOFTWARE_ENDSTOP_V
  #define MIN_SOFTWARE_ENDSTOP_W
#define MAX_SOFTWARE_ENDSTOPS
  #define MAX_SOFTWARE_ENDSTOP_X
  #define MAX_SOFTWARE_ENDSTOP_Y
  #define MAX_SOFTWARE_ENDSTOP_Z
  #define MAX_SOFTWARE_ENDSTOP_I
  #define MAX_SOFTWARE_ENDSTOP_J
  #define MAX_SOFTWARE_ENDSTOP_K
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

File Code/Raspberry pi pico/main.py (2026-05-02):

from machine import Pin, Timer, SoftI2C, ADC, PWM, UART
import ssd1306
import utime
import neopixel

# ================= CONFIGURATION =================
ADC_VOLT_PIN = 28
ADC_VOLT_2_PIN = 29
LED_PIN = 10
POT_T_ON_PIN = 26
POT_T_OFF_PIN = 27
NEOPIXEL_PIN = 23

SW_SPEED_ENABLE = 16
SW_PWM_ENABLE = 17

UART_TX_PIN = 4
UART_RX_PIN = 5
UART_BAUDRATE = 115200

# Shunt resistor value for current calculation (Ohms)
SHUNT_RESISTOR = 16.3

# Time parameters in microseconds (us)
T_OFF_MIN = 10      
T_OFF_MAX = 100     
T_ON_MIN = 3        
T_ON_MAX = 25       

SPEED_MIN_PERCENT = 50
SPEED_MAX_PERCENT = 200

# Ramp and smoothing parameters
SPEED_ALPHA = 0.2
SPEED_UP_LIMIT = 2.0    
SPEED_DOWN_LIMIT = 10.0 
DEADBAND = 0.8
SPEED_UPDATE_HZ = 20    

# Security & Regulation Parameters
LOW_VOLT_TIME = 1       # Seconds before triggering a hard fault
LOW_VOLT_FACTOR = 0.40  # Percentage of theoretical voltage for dynamic safety
V_MIN_SAFETY = 20.0     # Absolute minimum voltage floor (Merged security)

I_TARGET = 0.8          # Desired average current (Amps)
I_GAIN = 50.0           # Proportional gain for speed control
I_SHORT_CIRCUIT = 4.5   # Current threshold for physical contact detection

# ADC 1 Calibration (Pin 28)
CAL_ADC_VOLT_1 = 1.5
CAL_REAL_VOLT_1 = 43.4
CAL_FACTOR_1 = CAL_REAL_VOLT_1 / CAL_ADC_VOLT_1

# ADC 2 Calibration (Pin 29)
CAL_ADC_VOLT_2 = 1.5
CAL_REAL_VOLT_2 = 43.4 
CAL_FACTOR_2 = CAL_REAL_VOLT_2 / CAL_ADC_VOLT_2

NUM_SAMPLES = 10

# Stability parameters (V1)
V_STABLE_MARGIN = 0.85
V_DROP_THRESHOLD = -2.0
V_DROP_SENSITIVITY = 5.0

# ================= INITIALIZATION =================
i2c = SoftI2C(scl=Pin(19), sda=Pin(18), freq=100000)
display = ssd1306.SSD1306_I2C(128, 64, i2c)
display.rotate(2) 

np = neopixel.NeoPixel(Pin(NEOPIXEL_PIN), 1)

adc1 = ADC(ADC_VOLT_PIN)
adc2 = ADC(ADC_VOLT_2_PIN)

pot_t_on = ADC(POT_T_ON_PIN)
pot_t_off = ADC(POT_T_OFF_PIN)

pwm = PWM(Pin(LED_PIN))
uart = UART(1, baudrate=UART_BAUDRATE, tx=Pin(UART_TX_PIN), rx=Pin(UART_RX_PIN))

sw_speed = Pin(SW_SPEED_ENABLE, Pin.IN, Pin.PULL_UP)
sw_pwm = Pin(SW_PWM_ENABLE, Pin.IN, Pin.PULL_UP)

voltage_samples_1 = []
voltage_samples_2 = []

# ================= FUNCTIONS =================
def set_led(color):
    np[0] = color
    np.write()

def update_display(t_on_us, t_off_us, v_main, current_a, speed_percent):
    display.fill(0)
    display.text(f"ON:{int(t_on_us)}us", 0, 2, 1)
    display.text(f"OFF:{int(t_off_us)}us", 65, 2, 1)
    
    v_int = int(round(v_main))
    display.text(f"V: {v_int}V", 0, 15, 1)
    display.rect(60, 15, 65, 7, 1)
    v_fill = int(min(v_main, 100.0) / 100.0 * 65)
    display.fill_rect(60, 15, v_fill, 7, 1)
    
    display.text(f"I: {current_a:3.1f}A", 0, 30, 1)
    display.rect(60, 30, 65, 7, 1)
    i_fill = int(min(abs(current_a), 6.0) / 10.0 * 65)
    display.fill_rect(60, 30, i_fill, 7, 1)
    
    display.text(f"Speed: {speed_percent}%", 15, 50, 1)
    display.show()

# ================= MAIN PROGRAM =================
def main():
    state = {
        "tension_max": 0.0,
        "pwm_enabled": False,
        "smoothed_speed": 100.0,
        "last_speed_sent": 100.0,
        "old_int_sent": 100,
        "last_freq": -1,
        "fault_active": False,
        "low_volt_cnt": 0,
        "prev_v_avg": 0.0
    }

    def adc_timer_cb(timer):
        # High speed ADC sampling
        val1 = adc1.read_u16()
        v_adc1 = (val1 / 65535) * 3.3
        voltage_samples_1.append(v_adc1 * CAL_FACTOR_1)
        
        val2 = adc2.read_u16()
        v_adc2 = (val2 / 65535) * 3.3
        voltage_samples_2.append(v_adc2 * CAL_FACTOR_2)
        
        if len(voltage_samples_1) > NUM_SAMPLES: voltage_samples_1.pop(0)
        if len(voltage_samples_2) > NUM_SAMPLES: voltage_samples_2.pop(0)

    adc_t = Timer()
    adc_t.init(freq=1000, mode=Timer.PERIODIC, callback=adc_timer_cb)

    def control_loop(timer):
        if not voltage_samples_1 or not voltage_samples_2: return
        v1_avg = sum(voltage_samples_1) / len(voltage_samples_1)
        v2_avg = sum(voltage_samples_2) / len(voltage_samples_2)

        # Current Calculation (Differential voltage over shunt)
        current_amps = abs((v1_avg - v2_avg) / SHUNT_RESISTOR)

        # 1. Read Potentiometers & Compute PWM
        raw_off = pot_t_off.read_u16()
        raw_on = pot_t_on.read_u16()
        t_off_us = T_OFF_MIN + (raw_off * (T_OFF_MAX - T_OFF_MIN) / 65535.0)
        t_on_us = T_ON_MIN + (raw_on * (T_ON_MAX - T_ON_MIN) / 65535.0)
        
        t_off_s, t_on_s = t_off_us / 1_000_000.0, t_on_us / 1_000_000.0
        period = t_on_s + t_off_s
        if period <= 0: period = 0.000001
        
        f_target = int(1.0 / period)
        d_float = t_on_s / period
        d_u16 = int(d_float * 65535)

        pwm_sw = not sw_pwm.value()
        spd_sw = not sw_speed.value()

        # 2. PWM Frequency Update
        if 8 <= f_target <= 500000:
            if abs(f_target - state["last_freq"]) > 1:
                pwm.freq(f_target)
                state["last_freq"] = f_target

        # 3. Fault & LED Management
        if state["fault_active"]:
            set_led((255, 80, 0))
            pwm.duty_u16(65535) # Turn power off
            display.fill(0)
            display.text("!!! FAULT !!!", 15, 24, 1)
            display.text("LOW VOLTAGE V1", 10, 38, 1)
            display.show()
            if not pwm_sw:
                state["fault_active"] = False
                state["low_volt_cnt"] = 0
            return

        # LED color feedback based on active modes
        if pwm_sw and spd_sw: set_led((120, 0, 200))
        elif pwm_sw: set_led((255, 0, 0))
        else: set_led((0, 255, 0))

        # 4. Output Drive & Security Logic
        if pwm_sw:
            if not state["pwm_enabled"]:
                state["tension_max"] = v1_avg
                state["pwm_enabled"] = True
            
            pwm.duty_u16(65535 - d_u16)
            
            # Dynamic Voltage Security
            v_theo = state["tension_max"] * (1.0 - d_float)
            dynamic_thresh = max(V_MIN_SAFETY, v_theo * LOW_VOLT_FACTOR)
            
            if v1_avg < dynamic_thresh:
                state["low_volt_cnt"] += 1
                if state["low_volt_cnt"] > (LOW_VOLT_TIME * SPEED_UPDATE_HZ):
                    state["fault_active"] = True
                    uart.write("M25\n") # Halt G-code execution
            else:
                state["low_volt_cnt"] = 0
        else:
            pwm.duty_u16(65535)
            state["pwm_enabled"] = False

        # 5. Speed Logic (Hybrid Current/Voltage Regulation)
        target_v = 100.0
        if spd_sw and state["pwm_enabled"] and d_float < 0.98:
            
            # A. CRITICAL SECURITY (Absolute Priority)
            # Short circuit detected by current OR voltage floor breach
            if current_amps > I_SHORT_CIRCUIT or v1_avg < V_MIN_SAFETY:
                target_v = SPEED_MIN_PERCENT
                
            else:
                # B. CURRENT REGULATION (Proportional Loop)
                # Positive error = under target -> Speed up
                # Negative error = over target -> Slow down
                current_error = I_TARGET - current_amps
                target_v = 100.0 + (current_error * I_GAIN)
                
                # C. VOLTAGE SENSITIVITY (Delta V)
                # Penalize speed if voltage drops rapidly
                delta_v = v1_avg - state["prev_v_avg"]
                if delta_v < V_DROP_THRESHOLD:
                    target_v -= abs(delta_v) * V_DROP_SENSITIVITY

            # Clamp output within defined limits
            target_v = max(SPEED_MIN_PERCENT, min(SPEED_MAX_PERCENT, target_v))
        else:
            target_v = 100.0
        
        state["prev_v_avg"] = v1_avg

        # 6. Acceleration Ramp & Smoothing
        state["smoothed_speed"] = (SPEED_ALPHA * target_v) + (1.0 - SPEED_ALPHA) * state["smoothed_speed"]
        diff = state["smoothed_speed"] - state["last_speed_sent"]
        
        if abs(diff) > DEADBAND:
            step = (SPEED_UP_LIMIT if diff > 0 else SPEED_DOWN_LIMIT) / SPEED_UPDATE_HZ
            state["last_speed_sent"] += (step if diff > 0 else -step)
        else:
            state["last_speed_sent"] = state["smoothed_speed"]

        # 7. UART Transmission & Display Refresh
        current_spd_int = int(state["last_speed_sent"])
        if current_spd_int != state["old_int_sent"]:
            uart.write(f"M220 S{current_spd_int}\n")
            state["old_int_sent"] = current_spd_int

        update_display(t_on_us, t_off_us, v1_avg, current_amps, current_spd_int)

    # Main control loop timer
    main_t = Timer()
    main_t.init(freq=SPEED_UPDATE_HZ, mode=Timer.PERIODIC, callback=control_loop)

    try:
        while True:
            utime.sleep(1)
    except KeyboardInterrupt:
        adc_t.deinit()
        main_t.deinit()
        pwm.deinit()
        set_led((0,0,0))

if __name__ == "__main__":
    main()

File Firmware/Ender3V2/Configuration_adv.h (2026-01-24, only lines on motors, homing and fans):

#define E0_AUTO_FAN_PIN -1
#define E1_AUTO_FAN_PIN -1
#define E2_AUTO_FAN_PIN -1
#define E3_AUTO_FAN_PIN -1
#define E4_AUTO_FAN_PIN -1
#define E5_AUTO_FAN_PIN -1
#define E6_AUTO_FAN_PIN -1
#define E7_AUTO_FAN_PIN -1
#define CHAMBER_AUTO_FAN_PIN -1
#define COOLER_AUTO_FAN_PIN -1
#define HOMING_BUMP_MM      { 5, 5, 2 }       // (linear=mm, rotational=°) Backoff from endstops after first bump
#define HOMING_BUMP_DIVISOR { 2, 2, 4 }       // Re-Bump Speed Divisor (Divides the Homing Feedrate)
#define QUICK_HOME                            // If G28 contains XY do a diagonal move first
#define MICROSTEP_MODES { 16, 16, 16, 16, 16, 16 } // [1,2,4,8,16]

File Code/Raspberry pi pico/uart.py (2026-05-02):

from machine import Pin, UART, ADC
import time

# UART vers Marlin
uart = UART(1, baudrate=115200, tx=Pin(4), rx=Pin(5))

# Potentiomètre sur GP26 (ADC0)
pot = ADC(26)

# Trigger (pull-up)
trigger = Pin(16, Pin.IN, Pin.PULL_UP)

last_state = 1
last_speed = -1  # pour éviter spam UART

def set_fan(speed):
    uart.write(f"M106 S{speed}\n".encode())

while True:
    state = trigger.value()

    # Si bouton appuyé → ventilateur contrôlé par pot
    if state == 0:
        raw = pot.read_u16()              # 0–65535
        speed = raw * 255 // 65535       # 0–255

        # envoi seulement si changement significatif
        if abs(speed - last_speed) > 2:
            set_fan(speed)
            print("Fan:", speed)
            last_speed = speed

    # Si bouton relâché → vitesse fixe (ex 150)
    else:
        if last_speed != 150:
            set_fan(150)
            print("Fan fixe: 150")
            last_speed = 150

    last_state = state
    time.sleep_ms(100)

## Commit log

2026-01-19 Add PCB testing status note
    Add initial note about PCB testing status
2026-01-24 Add firmware modifications for Ender 3 V2
    Updated configuration files for firmware modifications including thermistor settings, thermal protections, fan configurations, and startup commands.
2026-02-01 Fix typo in PC/PS plate dimensions in README
2026-02-01 Add silicone seal cartridge to the materials list
2026-02-01 Update wire EDM post processor reference in README
    Updated the reference to the wire EDM post processor to include a link to the specific file for Fusion 360.
2026-03-15 Increase manual feedrate for extruder from 5 to 10

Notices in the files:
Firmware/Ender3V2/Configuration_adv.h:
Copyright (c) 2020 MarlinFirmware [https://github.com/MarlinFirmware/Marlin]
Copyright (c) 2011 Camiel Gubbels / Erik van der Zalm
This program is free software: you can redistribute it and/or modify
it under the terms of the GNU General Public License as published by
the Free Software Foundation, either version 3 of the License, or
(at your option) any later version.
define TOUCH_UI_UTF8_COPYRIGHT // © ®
